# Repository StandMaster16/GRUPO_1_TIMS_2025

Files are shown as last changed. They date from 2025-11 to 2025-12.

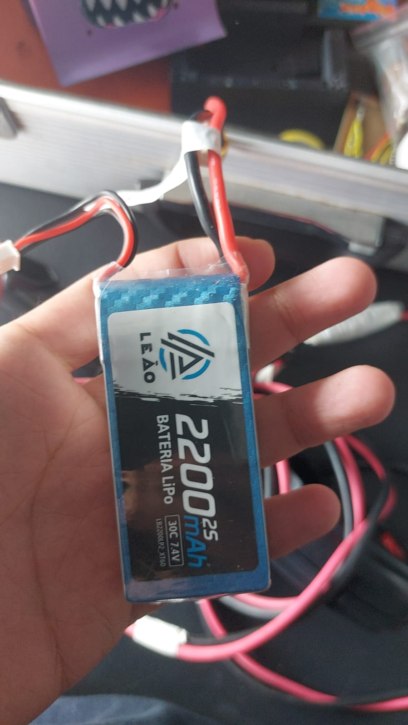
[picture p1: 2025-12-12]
electronics/img/Semana 1/bateria que vamos usar.jpg

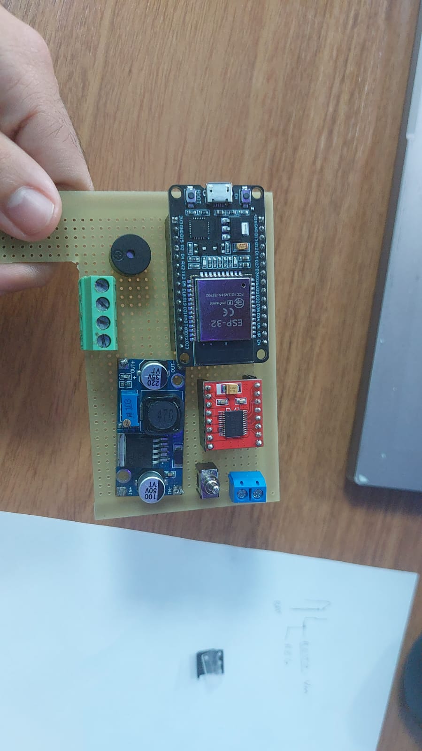
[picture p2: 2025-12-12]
electronics/img/Semana 7/primeiro arranjo.jpg

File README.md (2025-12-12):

# *Mini sumô - Sr. Batata*

Esse é o repositório online do projeto de mini sumô da equipe 1 do torneio interno do Grupo de Estudo Aplicado à Robótica (GEAR) em 2025.

## Equipe

- Gestão: Vitória Rodrigues
- Programação: Gabriel Matos
- Mecânica: David Praciano
- Eletrônica: Matheus Eduardo 
- Veterano: Vinicius Azevedo

## Organização dos Diretórios
```
GRUPO_1_TIMS/
|
├── code/                       # Implementação da programação
│
├── docs/                       # Documentação do código
│
├── electronics/                # Eletrônica do projeto
│
├── mechanics/                  # Mecânica do projeto
│
└── README.md --> ESTE ARQUIVO  # Resumo geral dos diretórios
```

Cada pasta contém um README interno com instruções específicas de uso, dependências e explicações específicas.

## Por quê "Sr. Batata"?

O ponto de partida do projeto mecânico foi a fase de brainstorming, que gerou inúmeras ideias de design. Para permitir a experimentação de todas as sugestões sem comprometer o protótipo base, a equipe decidiu por um robô desmontável.
Inspirado no conceito do brinquedo Toy Story, o robô foi batizado de "Sr. Batata", onde o chassi principal (a "batata") serviria como corpo base, e os acessórios seriam incrementos removíveis (como braços, chapéus e sapatos). A ideia era que, se um incremento não funcionasse em combate, bastaria desencaixá-lo e substituí-lo, agilizando a iteração de design.

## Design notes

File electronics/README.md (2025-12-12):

# Diretório de Eletrônica

## Como está organizado?

Em tese, tudo está na pasta `img/`, que contém um histórico de evolução do trabalho
de eletrônica do nosso mini sumô. Há um pequeno salto entre as semanas, por motivos
diversos, por exemplo: não tiramos foto de tudo. Porém, o que foi registrado e é 
pertinente, você com certeza vai encontrar lá.

## Um pouco sobre o circuito

O circuito do mini sumô "Sr. Batata" possui uma história interessante: Nasceu como um
simples arranjo de controlador, ponte H e motores, para uma máquina mortífera de 
controlador, ponte H, motores e algumas coisinhas.

## Como ele funciona?

### Componentes:

 - Dois motores n20 300 rpm
 - Uma ESP32
 - Uma ponte H TB6612FNG
 - Um buzzer passivo
 - Um controlador de tensão (AMS1117 ou o Buck Converter (ainda não foi decidido (11/12/25)))
 - Placa fenolite universal
 - Três KRE Borne
 - Barramento de pinos
 - Um switch alavanca

### Descrição:

A alimentação está ligada ao switch, a qual envia energia para a ponte H pela porta VM, que alimenta os motores A e B. A mesma alimentação é enviada ao regulador de tensão que converte 7.4v para 5v na porta VIM da ESP32. Os motores A e B estão ligados às respectivas portas OUT da ponte H, sendo as portas IN e PWM ligadas à ESP32. Por fim, o buzzer passivo conecta-se à ESP32

### Mural de conexões

- Positivo da Bateria -> L2 (switch)
- COM (switch) -> VM (TB6612FNG)
- A01 (TB6612FNG) -> Negativo do motor A
- A02 (TB6612FNG) -> Positivo do motor A
- B01 (TB6612FNG) -> Negativo do motor B
- B02 (TB6612FNG) -> Positivo do motor B
- D13 (ESP32) -> PWMA (TB6612FNG)
- D14 (ESP32) -> PWMB (TB6612FNG)
- D27 (ESP32) -> BI1 (TB6612FNG)
- D26 (ESP32) -> BI2 (TB6612FNG)
- D25 (ESP32) -> AI1 (TB6612FNG)
- D24 (ESP32) -> AI2 (TB6612FNG)

#### Para versão com AM1117 5V

- VIM (AMS1117) -> COM (switch)
- VOUT (AMS1117) -> VIM (ESP32)
- GND (AMS1117) -> GND (ESP32)
  
#### Para versão com Buck Converter

- IN+ -> COM (switch)
- IN- -> Negativo da Bateria
- OUT+ -> VIM (ESP32)
- OUT- -> GND (ESP32)

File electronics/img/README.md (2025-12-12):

# Diretório de Imagem de Eletrônica

O diretório está dividido em semanas, com registros visuais
de cada progresso feito em cada semana, além dos circuitos
feitos na plataforma CIRKIT IDE

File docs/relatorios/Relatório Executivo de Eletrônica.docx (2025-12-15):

RELATÓRIO DE ANDAMENTO DE ELETRÔNICA

RESPONSÁVEL TÉCNICO: Matheus Eduardo

PROJETO : Robô Mini Sumô Sr. Batata

PERÍODO: 28.11 a 12.12

CONCEITO E DEFINIÇÃO DA ARQUITETURA ELETRÔNICA

A premissa fundamental do robô Sr. Batata era a força para ser dominante no combate. Essa prioridade orientou a escolha de todos os componentes eletrônicos, buscando garantir a máxima potência e eficiência.

Pesquisa e Referências: O Matheus iniciou a fase de pesquisa nos sites das principais lojas de robótica do mundo (indicação do Vini), buscando inspiração e componentes em kits prontos e peças de mini sumô.

Escolha da Placa de Controle (MCU):

No dia 23/11, a equipe discutiu a escolha da placa de controle, com as seguintes considerações:

Opções | Análise | Decisão
STM32 | Conhecida como "o megazord das placas" por sua potência. Não havia experiência prévia em programação para ela | descartada.
ESP32 | Fortemente recomendada por um veterano (Célio) e mais familiar à equipe. | Selecionada. O repositório no Git foi criado utilizando a ESP32

SELEÇÃO DE COMPONENTES E TESTES INICIAIS

A escolha dos componentes foi fortemente baseada nas indicações de kits e peças das lojas de robótica que o Vinícius indicou.

Componentes | Especificação escolhida | Justificativa
motores | 2 modelos N20 de 300 RPM | Motores pequenos, com caixa de redução e os mais utilizados na categoria Mini Sumô.
Ponte H | TB6612FNJ | Embora necessitasse de um regulador de tensão (devido à bateria de alta voltagem), foi preferida em relação à L293D (que teria sido usada com 4 rodas).
Bateria | Lipo Battery 7.4v 2200 mAh | Recomendada por um veterano por proporcionar maior descarga de corrente. A tensão de 7,4V é enviada integralmente para os motores na potência máxima, garantindo o poder do robô.
Placa base | Placa fenolite (universal) perfurada de fibra de vidro | Usadas para montagem do circuito.
Conectores | XT60 (bateria), KRE borne (3) e barra de pinos | Para conexões de alimentação na placa principal

MARCOS DE TESTE (CIRCUITO EQUIVALENTE):

Data | Ação/Evento | Propósito e status
07.11 | Conclusão do esquema do circuito | O esquema do circuito já estava finalizado
07.11 | Testes dos motores no lab | Verificação funcional dos motores antes da montagem no chassi
14.11 | Montagem de um sistema eletrônico equivalente | Uso de componentes genéricos de laboratório para testes, simulando o sistema definitivo (motores, ESP, etc.)
02.12 | O Sr. Batata funciona (com circuito equivalente) | Comprovação da lógica do sistema antes da chegada/montagem das peças oficiais

DESAFIOS NA MONTAGEM OFICIAL

A transição para o circuito oficial foi marcada por desafios técnicos e de confiança, já que o responsável (Matheus) era da área de Programação, não de Eletrônica

Data | Evento/Desafio | Ação e impacto
Contínuo | Dificuldade na Disposição e Montagem: O responsável enfrentou dificuldades na disposição dos componentes no chassi. | O chassi de teste foi usado com componentes genéricos para validação da disposição.
14.11 | Aguardando Peças Oficiais: A equipe estava limitada, usando apenas peças do laboratório para montagem parcial. | Foco em montar o sistema eletrônico equivalente para adiantar os testes e a programação.
Todo o trajeto | Insegurança e Falta de Experiência (Soldagem): Matheus se sentiu inseguro com seu trabalho e inexperiente, especialmente na soldagem, que se tornou sua maior dificuldade. | A gestora ofereceu apoio contínuo. Ele recebeu ajuda e apoio de membros da própria equipe e de outras, o que aumentou sua confiança ao saber que outros programadores também atuavam na Eletrônica.
09.12 | Início da montagem do Circuito Oficial. | Com a confiança restabelecida e a lógica do circuito validada pelo modelo equivalente, Matheus iniciou a soldagem e montagem do circuito definitivo.
11.12 | Conclusão da Montagem do Circuito Oficial. | O circuito oficial foi finalizado a tempo para a integração com o chassi.

STATUS FINAL

O circuito equivalente cumpriu sua função de validar a lógica de potência e controle do Sr. Batata

Data | Marco alcançado | Estado atual (final) do projeto
11.12 | Circuito oficial finalizado | O circuito eletrônico principal está montado e pronto para ser integrado ao Chassi Oficial (que está em processo de impressão 3D, conforme o relatório de Mecânica)
12.12 | Integração física final e calibração de potência | O foco agora é na integração física com as partes mecânicas e no trabalho de Programação/Testes em campo

Anexos

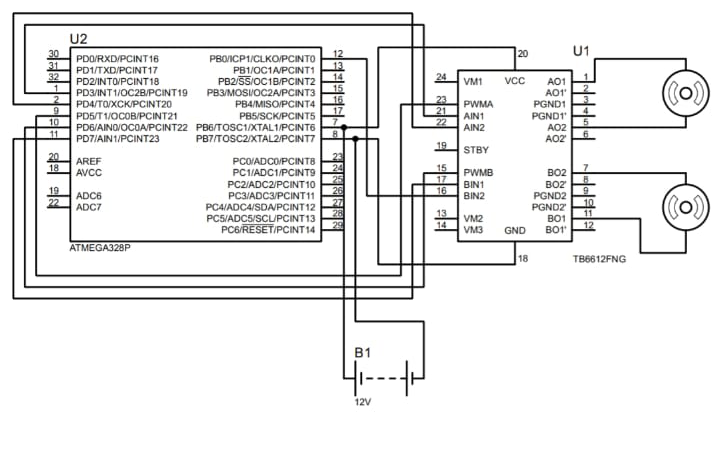
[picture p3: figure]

Anexo 1 - Circuito de esboço feito no proteus

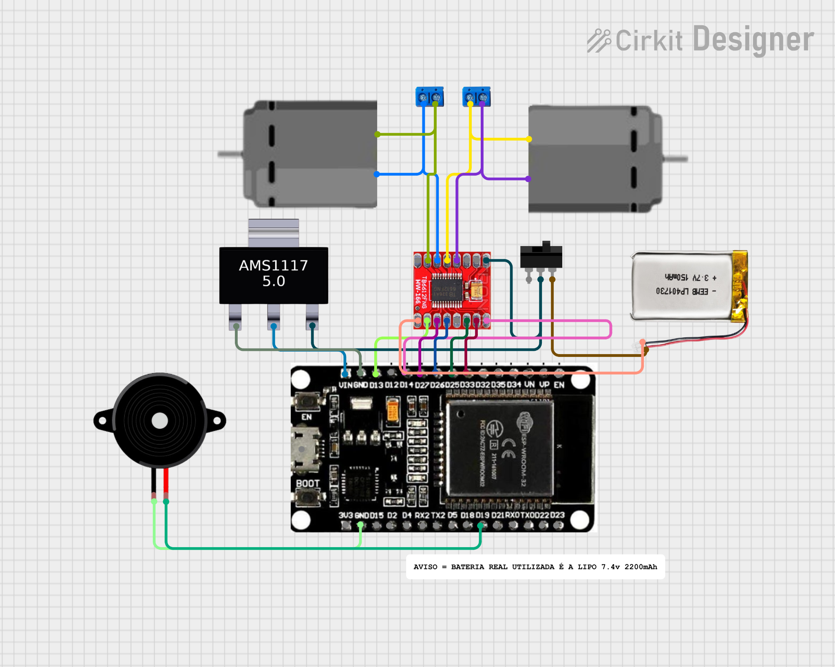
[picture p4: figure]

Anexo 2 - Modelo final 1 (usando AMS1117)

ESTE RELATÓRIO SERÁ ATUALIZADO CONTINUAMENTE PARA ACOMPANHAR A EVOLUÇÃO DA ÁREA ELETRÔNICA DO SR BATATA ATÉ O DIA DO TORNEIO (12.12)

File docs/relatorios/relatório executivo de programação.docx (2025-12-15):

RELATÓRIO DE ANDAMENTO DA PROGRAMAÇÃO

RESPONSÁVEL TÉCNICO:Couto Gabriel

PROJETO: Robô Mini Sumô Sr. Batata

PERÍODO: 28.11 a 12.12

PESQUISA, ALINHAMENTO E DEFINIÇÃO DO CONTROLE

O trabalho de programação começou com uma fase intensa de pesquisa nas duas primeiras semanas, utilizando os sites e vídeos indicados pelo Vinícius para definir a melhor arquitetura de código.

Mês | Ação geral
Outubro | O primeiro foco foi na escolha do controle. Embora a equipe inicialmente considerasse testar o uso de um aplicativo e um controle remoto, a decisão final foi priorizar o Controle Remoto para maior precisão e familiaridade, com o controle sendo reservado no dia 31 de Outubro.
Novembro | A equipe pegou uma ESP genérica para iniciar a fase de testes práticos do código. Em uma reunião de alinhamento entre as áreas, Praciano ajudou a definir a lógica de movimentação: o robô utilizaria o sistema Tank Drive, onde dois analógicos seriam usados para controlar a direção, com cada um controlando uma roda. Nesse mesmo dia, o código base já estava finalizado, embora apresentasse um erro de compilação no PlatformIO. A prioridade imediata passou a ser concluir o código de movimentação, buscando auxílio de Vinícius e outros veteranos para resolver a comunicação do controle com o ESP32.

DESENVOLVIMENTO DO CÓDIGO BASE E TESTES (10.11 a 17.11)

Um grande avanço ocorreu no dia 10 de novembro, quando o código base compilou 🙏. Com o problema de compilação resolvido, o foco passou para a validação funcional do sistema.

No dia 12 de Novembro, foi montado um circuito improvisado com LEDs para testar a comunicação entre a ESP e o controle. O teste foi bem-sucedido e o sistema se mostrou funcional. No entanto, foi notado que a deadzone do controle não estava ideal, sendo ajustada para evitar o drift. Infelizmente, dois LEDs foram queimados durante o processo.

Apesar do avanço, no dia 14 de Novembro, Gabriel ainda estava plotando o código na placa aos poucos, em processo de aprendizado. No dia 17 de Novembro, o programador ainda encontrava dificuldade em conectar o controle à placa microcontroladora.

O aprendizado técnico de Gabriel foi fortemente baseado na biblioteca Bluepad32 e no tutorial de Rachel De Barros (vídeo e site).

DETALHAMENTO DA LÓGICA DO CÓDIGO

O código desenvolvido por Gabriel utiliza a lógica de controle independente de cada motor. A seguir, uma análise do código funcional:

- Definição dos Pinos: O código inicia definindo a ligação física entre os pinos da ESP32 e a Ponte H.
- Controle de Movimento e Deadzone: Esta é a parte crucial do código. Ele usa a função ctl->axisY() para ler o movimento do analógico esquerdo.

AVANÇAR (roda esquerda):

if(ctl->axisY() >= 25) { // Se o analógico esquerdo for empurrado para frente

digitalWrite(A11, HIGH); // Define a direção (HIGH/LOW) para frente

digitalWrite(A12, LOW);

analogWrite(PWNA, 200); // Aciona o motor na velocidade 200

}

DEADZONE (garantia de parada)

if (ctl->axisY() > -25 && ctl->axisY() < 25) { // Se o analógico estiver na zona central

digitalWrite(A11, LOW); // Força a parada do motor

digitalWrite(A12, LOW);

}

Essa lógica de Deadzone (inicialmente em \pm 25, depois ajustada para \pm 75 no código final) foi fundamental para garantir que o robô pare completamente quando o analógico está em repouso, evitando o drift e garantindo maior controle no combate.

INTEGRAÇÃO E VALIDAÇÃO DO CIRCUITO EQUIVALENTE

Apesar das dificuldades iniciais com soldagem e o PlatformIO, a lógica do código foi validada em um sistema de teste:

- 29 de Novembro: Gabriel propôs usar uma Ponte H e motores antigos (genéricos) para testar o código, garantindo que a lógica de programação estivesse 100% funcional antes de Matheus integrar a eletrônica oficial.
- 05 de Dezembro: Durante os testes no circuito equivalente, o código foi validado com sucesso. No entanto, um imprevisto ocorreu (uma ponte H foi danificada, mas ressuscitou após um reparo) e foi observada uma inconsistência de propulsão (uma roda girando mais rápido que a outra), que a equipe se comprometeu a investigar na montagem final.
- 11 de Dezembro (Atualização do Código): O código mais recente já incorpora os aprendizados:
- A Deadzone foi ajustada de 70 para 75 e depois de 75 para 100, resolvendo o problema de drift do controle.
- Foi adicionada a Função Giro 360 (Zerinho Tokyo) no botão A, que inverte a direção de um dos motores, permitindo o giro rápido no próprio eixo, útil para reposicionamento tático.
- Foi implementado o Controle de Velocidade Variável (usando os botões Y para velocidade alta e X para velocidade baixa), permitindo que o robô use sua força total ou uma velocidade mais controlada.
- Foi adicionado um Sinal Sonoro (Buzzer) no botão B, que toca três vezes ao ser pressionado.

A área da programação do Sr Batata foi a com menos problemas e erros técnicos

por termos 2 programadores na equipe. Tivemos ajuda externa também e muito estudo por parte do Gabriel durante todo o andamento do projeto.

O restante do código na pasta de programação está totalmente comentado :

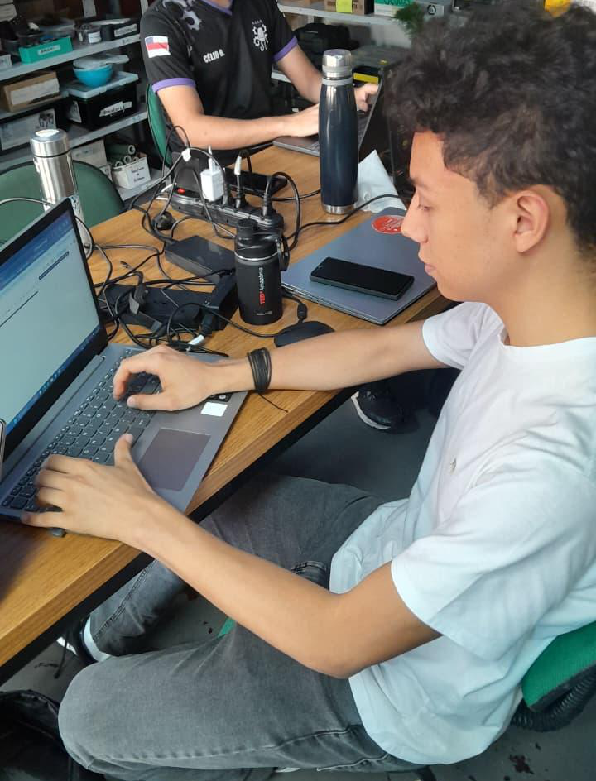
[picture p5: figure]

Gabriel trabalhando

ESTE RELATÓRIO SERÁ ATUALIZADO CONTINUAMENTE PARA ACOMPANHAR A EVOLUÇÃO DA ÁREA PROGRAMAÇÃO DO SR BATATA ATÉ O DIA DO TORNEIO (12.12)

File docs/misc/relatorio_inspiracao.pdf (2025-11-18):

UNIVERSIDADE DO ESTADO DO AMAZONAS ESCOLA SUPERIOR DE TECNOLOGIA GRUPO DE ESTUDOS APLICADOS À ROBÓTICA

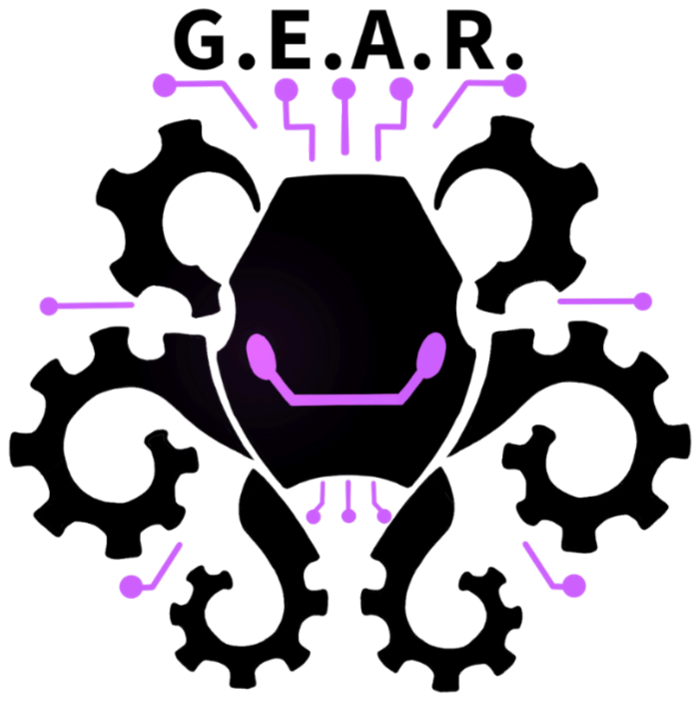
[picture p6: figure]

MINI SUMÔ

Manaus - AM
2025

RESUMO

O projeto teve como principal objetivo a confecção de robôs na modalidade mini

sumô, especificamente desenvolvidos para participar da competição Robocore 2025

em Brasília. Realizado por membros universitários, este projeto visou não apenas a

construção dos robôs, mas também proporcionar uma experiência prática e

aprofundada em áreas da engenharia, desde o trabalho em equipe, comunicação,

planejamento, design, testes até a execução. A participação na Robocore 2025

representou uma oportunidade valiosa, tendo em vista como sendo a primeira vez

que a liga acadêmica GEAR participa nesta modalidade. Além disso, foi uma

oportunidade valiosa para aplicar conhecimentos teóricos, desenvolver habilidades

multidisciplinares e fomentar o espírito de equipe e inovação entre os estudantes.

2

SUMÁRIO

3

### 1. INTRODUÇÃO

Este relatório detalha o desenvolvimento de dois robôs de mini sumô rádio

controlados de 500g, realizados por membros universitários do G.E.A.R.

(Grupo de Estudos Aplicados à Robótica). O objetivo principal foi projetar e

construir esses robôs para participar da competição Robocore Experience

2025. Este documento descreve todas as fases do projeto, desde o projeto

mecânico e eletrônico até a programação dos sistemas de controle. São

discutidos aspectos técnicos importantes, incluindo a comunicação Bluetooth

entre o microcontrolador e o controle remoto, os diagramas do circuito e as

considerações para o gerenciamento de energia. Em sua primeira

participação nesta categoria, a equipe conquistou o 15º e o 18º lugar de 20

competidores.

4

### 2. REFERENCIAL TEÓRICO

Mecânica:

- Modelagem do robô: Foi utilizado o software de CAD 3D Autodesk Inventor para realizar todas as medições dos componentes eletrônicos que seriam utilizados, o esboço do projeto e, por fim, a sua modelagem final. Aspectos de como os componentes seriam organizados para que o centro de massa fosse concentrado um pouco mais à frente do meio do robô, como estaria a sua distribuição de peso e o custo do material que seria utilizado foram considerados.
- Impressão do robô: Nosso laboratório possui a impressora 3D da Creality, portanto, foi usado o software fatiador Creality Print. Nele foram definidos parâmetros como o tipo de preenchimento, a forma da impressão e o tipo de material. Nesta etapa houve várias tentativas de impressão até chegar ao modelo final.
- Chapa Metálica: Para a construção da chapa foi usado um material mais resistente, uma lâmina de aço de mais ou menos 20cm x 20cm fora utilizado para a produção da mesma. Utilizando ferramentas como uma tesoura de cortar para reduzir suas dimensões, uma mini retifica para retirar as rebarbas e lixar a chapa para deixá-la mais fina.
Este método, revisado depois da competição da RoboCore Experience, tornou-se inviável a nível de competição - visto que utilizam-se chapas fabricadas exclusivamente para robôs sumôs mini.

Eletrônica:

- Componentes utilizados no Mini Robô Sumô
- Microcontrolador ESP 32
- Baterias Li-ion 7,4v 3300mah Modelo 18650 Recarregável
- Drive Motor Ponte H Dupla L298N
- Motores JGA 25-370
- Buzzer Ativo 5v
- Chave Interruptor
- O projeto do mini robô sumô rádio controlado utiliza como núcleo de processamento a placa ESP32, um microcontrolador de arquitetura Xtensa dual-core, amplamente empregado em sistemas embarcados

5

devido à sua conectividade Wi-Fi e Bluetooth integrada, capacidade de processamento e número elevado de GPIOs (General Purpose Input/Output).

- A alimentação elétrica do sistema é gerenciada por meio de uma ponte H L298N, a qual, além de controlar a direção e a velocidade dos motores DC, possui um regulador de tensão interno pré-ajustado para fornecer 5
V. Esse regulador é responsável por alimentar a ESP32 e periféricos, como o buzzer ativo, que atua como sinalizador sonoro para indicar tanto a energização do circuito quanto a conexão estabelecida entre o robô e o controle remoto.
- Para tração, foram utilizados motores JGA, conectados diretamente à bateria Li-Po de 7,4 V, garantindo torque e velocidade adequados às exigências da competição. O controle do robô é realizado através de gamepads de PS4 e Xbox, via comunicação Bluetooth, em conformidade com as normas especificadas no regulamento do campeonato.
- A integração eletrônica descrita fornece a base para a atuação da equipe de programação, responsável pela implementação dos algoritmos que interpretam os sinais enviados pelos controles e convertem essas entradas em comandos para a ponte H e demais atuadores. Nesse contexto, podem ser empregados algoritmos de controle, como o BluePad 32 , para otimizar a resposta dos motores, além de rotinas para gerenciamento de estados do robô, comunicação Bluetooth e tratamento de eventos. Assim, o trabalho conjunto entre hardware e software assegura que o mini robô atue de forma eficiente, responsiva e em conformidade com os parâmetros da competição.

Programação:

- Sistema embarcado (Parte do Software): o sistema embarcado atuou como um receptor e interpretador dos comandos em tempo real. A programação foi robusta o suficiente para receber dados por rádio frequência, os processar rapidamente e acionar os atuadores (Motor e Buzzer) sem atrasos perceptíveis para o operador. Isso envolve a configuração de interrupções e o gerenciamento eficiente do loop principal no código para garantir o retorno. A escolha da linguagem C foi a ideal para essa atividade devido a eficiência e controle de hardware (ESP32).

6

- Comunicação via Rádio Frequência: o ESP32 possui um módulo Wi-Fi e Bluetooth integrado que pode ser configurado para comunicação por rádio frequência, como usamos controle de Xbox não houve a necessidade do módulo Wi-Fi, assim trabalhamos somente com o bluetooth. Estabelecemos um protocolo de comunicação entre o transmissor (Controle de Xbox) e o receptor (ESP32 do robô) para garantir que os dados fossem enviados e recebidos de forma decifrável. Uma comunicação exclusiva entre dois dispositivos, com o transmissor e receptor pelo emparelhamento via ID (Identificador do Transmissor), evitando interferência externa.
- Utilização de biblioteca para comunicação bluetooth da ESP32 com o controle: A biblioteca utilizada foi a Bluepad 32, do autor Ricardo Quesada, que permitiu que a placa pudesse se comunicar via Bluetooth com o controle de Xbox e de PS4. Essa biblioteca permite que placas como ESP32, ESP32 da linha S e Arduino, possam se conectar a diversos periféricos, como mouses, teclados e controles de Xbox, PS e Nintendo Switch, para diversos fins.

### 3. METODOLOGIA

A metodologia adotada para a construção dos robôs mini sumo foi estruturada para garantir um processo organizado e eficiente, desde o planejamento inicial até os ciclos de testes e melhorias.

### 1. Etapas de Desenvolvimento

O desenvolvimento dos robôs mini sumo seguiu um fluxo de trabalho interativo e adaptativo, buscando otimizar a colaboração da equipe e o progresso do projeto. As principais etapas incluíram:

### 1. Planejamento Inicial: Definição dos objetivos do projeto e das

estratégias gerais.

### 2. Levantamento de Requisitos: Detalhamento das funcionalidades e

especificações de cada robô.

### 3. Cronograma e Divisão de Tarefas 4. Projeto Mecânico: Concepção e construção da estrutura física do

mini robô sumô.

7

### 5. Projeto Eletrônico: Desenvolvimento dos circuitos e seleção dos

componentes eletrônicos.
6. Programação: Criação dos algoritmos de controle e inteligência.

### 2. Levantamento de Requisitos

A fase de levantamento de requisitos teve início com uma reunião entre todos os integrantes da equipe de mini sumo. Durante esse encontro, foram realizadas trocas de ideias e discussões para definir as especificações e funcionalidades de cada um dos quatro robôs mini sumo a serem construídos. O objetivo inicial era desenvolver dois mini sumôs RC e dois mini sumôs autônomos. Entretanto, ao final do projeto, foi possível desenvolver a construção de dois mini sumôs RC.

### 3. Cronograma e Divisão de Tarefas

O planejamento inicial incluiu a elaboração de um cronograma de atividades com base nas discussões da reunião inicial. Embora ferramentas como o Trello tenham sido consideradas pela gestão, a equipe adaptou-se a um acompanhamento direto via WhatsApp devido a dificuldades de uso por parte de alguns membros.

A equipe, composta por cinco membros e um líder, passou por uma reestruturação para otimizar a distribuição de responsabilidades:

- Divisão Inicial: Duas duplas e uma área de mecânica.
- Divisão Final por Áreas de Especialização: Eletrônica, Programação e Mecânica.

O monitoramento das atividades e o acompanhamento do progresso eram realizados por meio de relatórios semanais enviados via WhatsApp. Estes relatórios continham os seguintes tópicos:

- O que fizeram durante a semana: Detalhamento das atividades concluídas.
- O que irão fazer na próxima semana: Planejamento das próximas tarefas.
- Bloqueios: Identificação de qualquer impedimento ou desafio enfrentado.
- Andamento do projeto: Resumo geral do progresso.

O líder da equipe também atuava ativamente no monitoramento do projeto, prestando apoio e tirando dúvidas dos membros, garantindo que os obstáculos fossem superados rapidamente.

8

### 4. Projeto Mecânico

O projeto mecânico foi fundamental para a concepção e materialização da estrutura física dos robôs mini sumô. Esta etapa concentrou-se em um estudo aprofundado dos chassis tipicamente utilizados em competições dessa modalidade, buscando as melhores práticas para:

- Equilíbrio e Desenvolvimento: Foram exploradas estratégias para garantir a estabilidade do chassi, crucial para um bom desempenho em combate, permitindo que o robô mantivesse sua posição e executasse manobras eficazmente.
- Acoplamento de Componentes: A estrutura foi projetada para permitir o acoplamento seguro e otimizado de todos os componentes eletrônicos e mecânicos (motores, baterias, sensores, etc.), visando uma distribuição de peso eficiente e um design compacto.
- Controle do Atrito: Analisou-se o atrito gerado entre o robô e a arena, bem como entre os próprios componentes, para otimizar a tração e a movimentação do mini sumo, influenciando diretamente sua capacidade de empurrar o oponente.

### 5. Projeto eletrônico

O sistema eletrônico do mini robô sumô é responsável por receber os comandos do piloto via rádio, acionar os motores e executar as manobras previstas para o combate. O projeto foi desenvolvido em conformidade com as regras da competição, priorizando eficiência, baixo consumo de energia e resposta rápida.

Inicialmente, a dupla responsável simulou um circuito completo para o robô no software Fritzing, incluindo um módulo Regulador de Tensão Step Down LM2596.

9

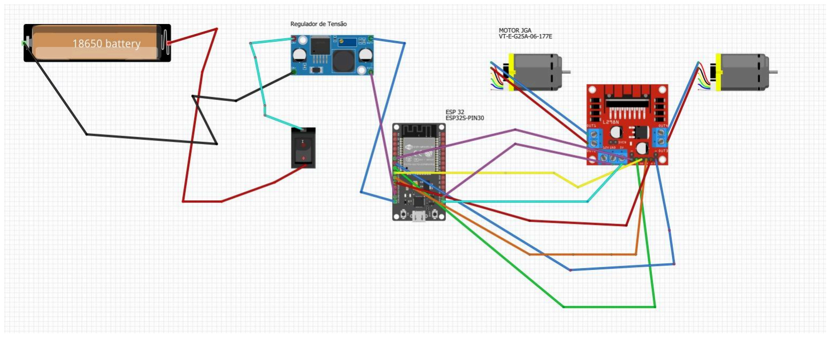
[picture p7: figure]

Dois pontos importantes considerados no projeto eletrônico do mini robô sumô foram:

1.Compatibilidade com as regras da competição: Todos os componentes e a disposição do circuito foram escolhidos para respeitar os limites de peso, dimensões e requisitos de segurança.

2.Integração dos componentes eletrônicos: Garantir a correta integração entre todos os componentes, como a bateria, o driver de motores, os motores DC e o microcontrolador ESP32. Essa integração assegura que as tensões e correntes estejam dentro dos limites operacionais de cada módulo, evitando sobrecargas, aquecimento excessivo ou falhas de comunicação.

Entretanto, ao longo da competição, foi observado que a ESP 32 suportava a tensão fornecida diretamente pela bateria e que o regulador gerava perdas e aumentava o peso do robô. Após análise, optou-se pela sua remoção, simplificando o circuito, diminuindo o número de conexões e eliminando um ponto potencial de falha.

### 6. Programação

A estrutura da lógica de programação foi simples, sendo a inteligência do robô residindo inteiramente na programação baseada na linguagem C/C++ que foi desenvolvida para o ESP 32, utilizando a Arduino IDE. Após estudos, a biblioteca bluepad 32 se mostrou mais versátil por permitir ao microcontrolador se conectar com uma gama maior de periféricos, ao contrário de bibliotecas como a PS4 Controller, que, como o nome sugere, só permite a conexão de controles de PS4.

Por conseguinte, a escolha da Arduino IDE também se deu pela sua facilidade de uso e fácil configuração, ao invés do VS Code (que aliás usa o framework da Arduino IDE através do PlataformIO para programação em Arduino) e da ESP-IDF, que apesar de permitir um controle maior do hardware, requer programação mais avançada e refinada, ou seja, de mais baixo nível de abstração.

Logo, por se tratar de uma biblioteca versátil, o controle do robô tornou-se mais fácil, pois não houve necessidade de projetar um joystick do zero, sendo utilizável no lugar controles populares de Xbox Series e Playstation 4, que são permitidos pelo regulamento da competição.

10

### 4. DESENVOLVIMENTO

- Estrutura mecânica

A modelagem do chassi em seu início foi trabalhosa por dois motivos principais: o tamanho dos motores JGA25-370 e da falta de um Placa de Circuito Impresso (PCI).

Um motor JGA25-370 combinado com o suporte e a roda somavam quase 100mm de comprimento, então um design para o robô partiu de uma ideia não convencional que foi deixá-lo disposto de uma forma antiparalela em relação ao outro motor. Isso possibilitou a integração dos motores, porém resultou em um centro de massa que classifica-se como um equilíbrio estático instável. A solução para amenizar tal impacto foi modelar o encaixe das baterias na frente do robô, projetando ele pra frente.

A falta de uma PCI resultou em um chassi bastante robusto e sem contornos, tendo uma aparência bastante cúbica e deixando-o no limite de seu peso (497g) e área (97mm x 95mm) prevista no edital: 500g e 100mm x 100mm.

Apesar disso, foi possível modelar, fatiar, imprimir e montar o robô sem muitos problemas. O espaço exigido pelos componentes foi atendido pela modelagem do robô e o problema do centro de massa foi diminuído pelo contrapeso das baterias e chapa metálica.

- Arquitetura eletrônica

A arquitetura eletrônica do mini robô sumô foi concebida de forma a garantir simplicidade. O sistema é composto pelo microcontrolador ESP32, responsável pelo processamento central e pela comunicação Bluetooth com os controles de PS4 e Xbox; pela ponte H L298N, utilizada para o acionamento bidirecional dos motores DC; pelos motores JGA25-370 (posteriormente reavaliados quanto ao peso); pela bateria Li-ion 7,4 V , que fornece a energia principal; além de um buzzer ativo 5 V, empregado como sinalizador sonoro, e de uma chave interruptora para desligar o circuito do robô .

- Sistema de alimentação

O sistema do robô é alimentado por uma bateria Li-Po de 7,4 V, utilizada tanto para a lógica quanto para a potência dos motores. A tensão da bateria é

11 aplicada diretamente ao terminal VMOT do driver L298N, responsável por alimentar os motores de corrente contínua. Para a parte lógica, não foi necessário o uso de reguladores externos, pois o próprio driver disponibiliza uma saída interna regulada de 5 V, utilizada para alimentar a ESP32. Dessa forma, a alimentação é simplificada, reduzindo a quantidade de componentes.Além disso, todos os terminais de GND foram conectados em um ponto comum, garantindo a referência elétrica única para o correto funcionamento do circuito e a comunicação estável entre ESP32 e driver.

- Lógica de Programação e Integração entre os Sistemas

Como discutido anteriormente, a lógica foi dividida da seguinte forma:

### 1. Comunicação por Rádio Controlado (Controle de Xbox)

O coração da operação do robô é a comunicação sem fio com o controle de Xbox. A programação ficou focada em:

### 1.1. Inicialização e Emparelhamento: O código inicia o módulo de

comunicação (Bluetooth Low Energy - BLE). Uma rotina foi implementada para procurar e estabelecer a conexão com o controle, quando a conexão é feita, o buzzer emite um som específico, fornecendo um feedback audível.

### 1.2. Decodificação de Dados: Uma vez conectado, o ESP32 envia dados

pelo controle. A programação inclui um parser para decodificar esses comandos, interpretando os estados dos botões e os valores dos eixos analógicos (joysticks) para determinar a direção e a velocidade dos motores. Tipo, os valores de X e Y de um joystick eram mapeados para o controle diferencial dos motores.

### 1.3. Restrição de Controle: Uma das principais regras da competição é

a de que o controle não pode se conectar a nenhum outro robô a não ser o do competidor. Esta restrição foi desenvolvida a partir da utilização mais avançada da biblioteca, através de uma função específica que lê um determinado parâmetro do periférico (o escolhido no projeto foi o PID – Product Identification), e o compara com o do periférico escolhido como único a ser pareado e retorna erro se for um dispositivo diferente, senão, o periférico irá se conectar e ter controle das funções. Foram realizados testes com resultados satisfatórios, nos quais controles diferentes do que havia sido pré-determinado via código se conectaram, mas não exerciam nenhum controle sob o robô, confirmando a restrição.

### 2. Controle de Atuadores (Motores N20)

12

A lógica de movimentação do robô foi desenvolvida para ser precisa e responsiva aos comandos do controle:

### 2.1. Mapeamento de Comandos: Os valores decodificados dos

joysticks são traduzidos em sinais PWM (Pulse Width Modulation) para cada motor. Houve a implementação de um algoritmo para converter as entradas X e Y do joystick em velocidades individuais para o motor esquerdo e direito, permitindo manobras como avançar, recuar, girar no próprio eixo e realizar curvas.

### 2.2. Controle de Velocidade e Direção: A programação manipula os

pinos GPIO conectados aos drivers de motor para controlar a direção de rotação e utiliza as funções de analogWrite() para variar o ciclo de trabalho do PWM, controlando a velocidade de forma suave e proporcional à inclinação do joystick.

### 3. Feedback Sonoro (Buzzer)

O buzzer foi programado para fornecer informações importantes como previsto pelo edital:

### 3.1. Indicação de Ligado: Ao energizar o robô, o código inicia com um

som tocado pelo buzzer, confirmando que o sistema embarcado está ativo.

### 3.2. Confirmação de Conexão RC: Conforme mencionado, um som

distinto é emitido quando o robô se conecta ao controle de Xbox, indicando que está pronto para receber comandos.

- Desafios enfrentados e soluções aplicadas

### 1. Problemas de Conectividade: Em alguns momentos, a conexão por rádio

frequência se mostrava instável. Para resolver isso, retardamos o acionamento do sinal feito por um dos joysticks para ganharmos tempo de conexão. Ajustes nos parâmetros de emparelhamento também foram explorados.

### 2. Latência na Comunicação RF: Inicialmente, notamos um pequeno atraso

entre o comando no controle e a resposta do robô. A solução envolveu a otimização do loop principal do código e também o “ponto morto” garantindo que a leitura dos dados por RF fosse prioritária e não fosse bloqueada por outras operações. Além disso, ajustamos a frequência de atualização dos dados no lado do controle e a taxa de amostragem no ESP32.

13

### 5. RESULTADOS PRELIMINARES

- Mecânica
O início dos testes para observar os resultados preliminares foi de extrema importância para analisar todo o desempenho físico por parte do mini robô sumô, nesta fase buscava-se:
1. Chassi: analisar se o material usado para modelar o robô suportaria o estresse mecânico que o mesmo estava sujeito, realizando testes que simulavam o peso do robô adversário. O resultado foi satisfatório, o material usado mostrou-se resistente aos embates em diferentes tipos de materiais usados;

### 2. Chapa metálica: testemunhar se a chapa estava adequada para oferecer

uma melhor rampagem e se estava bem fixada. Os testes haviam mostrado que o robô conseguia rampar os robôs simulados por objetos que haviam no laboratório;

### 3. Espaço para os componentes: testar se o espaço fornecido para os

componentes estava adequado a modo que não houvesse danos e se os mesmos não alterariam o centro de massa do robô. A observação preliminar ressaltou a dificuldade de organizar a quantidade de componentes eletrônicos dentro do chassi permitido pelo edital, resultando em um interior poluído visualmente, porém não o impedia de funcionar como o esperado.

- Eletrônica

Nos resultados preliminares, observou-se que a montagem eletrônica do mini robô sumô apresentou algumas limitações durante a competição. A ausência de uma placa de circuito impresso dificultou a organização do sistema elétrico, pois o uso excessivo de jumpers ocasionava falhas de contato.Esse tipo de montagem, embora funcional nos testes iniciais, não se mostrou o mais adequado para as exigências da competição, evidenciando a necessidade de um circuito otimizado e mais robusto para garantir maior confiabilidade.

Outro ponto relevante foi a escolha dos motores JGA25-370. Apesar de serem motores de alto torque, mostraram-se desvantajosos para a categoria de mini sumô, pois apresentavam peso elevado em relação ao tamanho reduzido e à agilidade exigida nos combates. Essa experiência permitiu concluir que a utilização de motores N20, mais leves e compactos, seria uma

14 alternativa mais adequada, equilibrando torque e velocidade com menor impacto no peso total do robô.

Para as próximas etapas, pretende-se redesenhar o sistema em uma placa dedicada, revisar a seleção dos motores e aprimorar a integração dos componentes, visando maior eficiência e competitividade.

- Programação

A fase de resultados preliminares foi crucial para validar a lógica de programação desenvolvida para o robô. Após a conclusão da montagem e da primeira versão do firmware, iniciamos os testes funcionais que focaram em:

### 1. Resposta aos Comandos por Rádio Controlado: Verificamos a latência

e a confiabilidade da comunicação entre o controle de Xbox e o ESP32. Ajustes na frequência de envio de comandos pelo controle e otimização na rotina de leitura e decodificação no robô foram implementados para minimizar qualquer atraso perceptível. Testes de alcance da comunicação também foram realizados para simular as condições da arena.

### 2. Controle de Motores: Realizamos testes para calibrar o mapeamento dos

valores do joystick para o PWM dos motores. O objetivo foi alcançar uma resposta de aceleração e direção suave e previsível. Inicialmente, observamos que o robô realizava movimentos bruscos. Para solucionar isso, implementamos uma curva de resposta não-linear no código, que suaviza as transições de velocidade e permite manobras mais precisas e controladas, essenciais para empurrar o oponente.

### 3. Feedback Sonoro do Buzzer: Confirmamos que os bipes de "ligado" e

"conectado" eram claros e funcionavam conforme programado, fornecendo um feedback audível e instantâneo.

### 4. Comportamento em Perda de Sinal: A perda de conexão foi o maior dos

problemas que tivemos, não solucionamos a perda de conexão, mas contornamos tardando essa perda de conexão. Como as lutas finalizaram em poucos segundos, não tivemos problemas por perda de conexão no campeonato.

15

### 6. RESULTADOS FINAIS

A participação da equipe na Robocore Experience 2025 resultou no 15º e 18º lugares, um desempenho que reflete o processo de aprendizado da equipe em sua primeira competição. O controle via Bluetooth e a resistência da estrutura mecânica foram pontos positivos. No entanto, o resultado foi negativamente impactado pelo peso excessivo dos motores JGA25-370 e pela montagem eletrônica com jumpers, que se mostrou pouco confiável durante os combates, indicando a necessidade de uma placa de circuito impresso.
A competição expôs uma lacuna entre o planejamento e o desempenho prático. O projeto inicial foi reduzido pela metade, focando em dois robôs rádio controlados em vez de quatro. A chapa metálica, eficaz em testes de laboratório, não performou bem contra adversários reais, e o sucesso na implementação da biblioteca de software Bluepad 32 contrasta com as dificuldades de hardware. Isso demonstrou a importância da adaptação e revelou pontos fortes e fracos do projeto.
Os aprendizados obtidos foram o resultado mais importante da experiência. Ficou claro que, para o futuro, é crucial otimizar o peso utilizando motores mais leves como o N20, desenvolver uma placa de circuito impresso para maior confiabilidade e aprimorar o design mecânico para um centro de massa mais estável. A gestão do projeto também foi identificada como um ponto de melhoria. A competição funcionou como um diagnóstico, oferecendo um direcionamento claro para futuras melhorias técnicas e organizacionais.

### 7. CONCLUSÃO

O desenvolvimento do mini sumô foi uma experiência desafiadora e, ao mesmo tempo, muito enriquecedora para a equipe. Tivemos que lidar com a dificuldade de conciliar os horários de todos, já que muitos tinham aulas e provas no mesmo período. Isso atrasou algumas etapas e, em certos momentos, quase paralisou o andamento do projeto. Esse desafio nos mostrou a importância de planejar melhor o tempo e buscar alternativas.

A participação na competição foi um ponto marcante, pois permitiu colocar em prática todo o esforço investido e visualizar, de forma clara, os resultados do nosso trabalho. Durante o torneio, conseguimos perceber os aspectos que precisam de melhorias, essa experiência prática foi fundamental para entender onde podemos evoluir, seja na parte técnica, como ajustes de programação e mecânica.

16

Mais do que os resultados, o aprendizado coletivo foi o maior ganho. A comunicação, a cooperação e a superação das dificuldades mostraram o potencial da equipe para enfrentar novos desafios. A competição não foi apenas uma oportunidade de mostrar o robô, mas também de crescer como grupo e já pensar em melhorias para futuros projetos, com mais foco, organização e confiança.

### 8. REFERÊNCIAS

QUESADA, Ricardo. bluepad32: Joystick, Gamepad and Bluetooth library for
ESP32 | and | Arduino | boards. | [Código-fonte]. | Disponível | em:
https://github.com/ricardoquesada/bluepad32. Acesso em: 30 abr. 2025.

SANTOS, Rui; SANTOS, Sara. ESP32 Pinout Reference: GPIOs. Random
Nerd | Tutorials, | [S. | l.], | 16 | jan. | 2024. | Disponível | em:
https://randomnerdtutorials.com/esp32-pinout-reference-gpios/. Acesso em: 29 mai. 2025.

DE BARROS, Rachel. Connect Your Game Controller to an ESP32: The Complete Guide. Rachel De Barros, [S. l.], [2025]. Disponível em: https://racheldebarros.com/connect-your-game-controller-to-an-esp32/. Acesso em: 15 abr. 2025.

NERY, GUSTAVO. Guia Definitivo de uso da Ponte H L298N. Blog Eletrogate,
5 | mar. | 2020. | Atualizado | em: | 1º | set. | 2022. | Disponível | em:
https://blog.eletrogate.com/guia-definitivo-de-uso-da-ponte-h-l298n. Acesso em: 20 mai. 2025.

Manaus, 7 de setembro de 2025

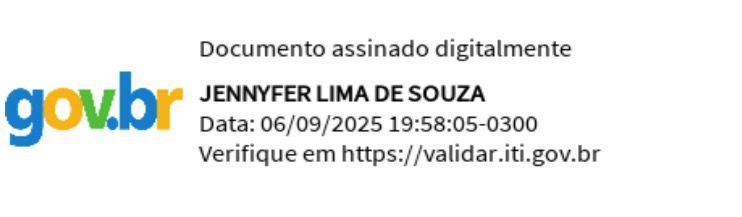
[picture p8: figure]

________________________________________________ Jennyfer Lima De Souza

17

________________________________________________ Cássio Pacheco Reis Lima

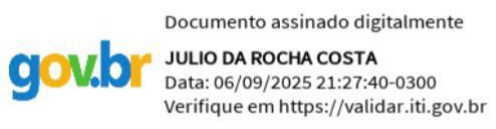
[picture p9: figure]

________________________________________________ Júlio Da Rocha Costa

________________________________________________ Ana Paula Monteiro Coelho

________________________________________________ Suely Amélia Casilla Nina

________________________________________________ Gabriele Lima De Souza

________________________________________________ Eduardo Araújo De Oliveira

___________________________________________________

18

Almir Kimura Junior

___________________________________________________ Samya De Castro Carvalho

19

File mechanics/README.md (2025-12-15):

## Diretório de Mecânica

Aqui se encontra imagens e os modelos 3D do Sr. Batata

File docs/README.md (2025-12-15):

## Diretório de Documentação

Este diretório tem como objetivo documentar o projeto do código do robô do seu grupo. É o relatório de todo o projeto.
Made by Vitória

O código implementado pode ser visto em: [`code`](../code).

## Estrutura do diretório

- `/atas` - Aqui fica as atas
- `/img` - Aqui fica mídias diversas
- `/misc` - Aqui fica alguns documentos que não se encaixam em nenhuma classificação
- `/relatorios` - Aqui fica os relatórios de cada sub-equipe do projeto
- `/sprint` - Aqui fica os sprints feitos com o Célio e a equipe

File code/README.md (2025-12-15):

## Diretório de Programação

Esse diretório está estruturado para um projeto PlatformIO, no entanto, a plataforma utilizada foi o ArduinoIDE
Por conta disso, somente a pasta `/src` foi modificada propriamente

## Estrutura de Diretórios

O projeto está organizado da seguinte forma:

```
code/
├── .pio/               # Arquivos de compilação e firmware (gerado automaticamente, não está no git)
├── .vscode/            # Configurações do editor Visual Studio Code (gerado automaticamente, não está no git)
├── include/            # Arquivos de cabeçalho (.h) globais do projeto
├── lib/                # Bibliotecas privadas (específicas do projeto) e externas
├── src/                # Arquivos de código-fonte (.c, .cpp) da aplicação
├── test/               # Testes unitários para validação do código
├── platformio.ini      # Arquivo de configuração principal do PlatformIO
└── README.md           # Este arquivo de documentação
```

### Descrição

  * `├── .pio/`

      * Este diretório é gerenciado pelo PlatformIO e contém os arquivos de compilação, dependências baixadas e o firmware final (`.bin` ou `.hex`). **Ele deve ser ignorado pelo sistema de controle de versão (ex: .gitignore).**

  * `├── .vscode/`

      * Contém as configurações específicas para o editor Visual Studio Code, como definições do IntelliSense. Também é gerenciado automaticamente.

  * `├── include/`

      * Use este diretório para arquivos de cabeçalho (`.h`, `.hpp`) que precisam ser compartilhados entre diferentes partes do seu código-fonte em `src/`. Um exemplo clássico é um arquivo `config.h` com definições de pinos e constantes globais.

  * `├── lib/`

      * Local ideal para bibliotecas. Cada biblioteca deve estar em sua própria subpasta (ex: `lib/MySensorLib/`). O PlatformIO automaticamente compila e vincula essas bibliotecas ao projeto. É perfeito para encapsular e reutilizar código.

  * `├── src/`

      * O coração da sua aplicação. O código-fonte principal (`.c`, `.cpp`) reside aqui. O arquivo `main.cpp` (ou `main.c`), que contém as funções `setup()` e `loop()`, é o ponto de entrada do programa.

  * `├── test/`

      * Destinado aos testes unitários. O [PlatformIO Test Runner](https://docs.platformio.org/en/latest/advanced/unit-testing/index.html) procura e executa os testes localizados aqui, ajudando a garantir a qualidade e a confiabilidade do código.

  * `└── platformio.ini`
      * Este é o arquivo de configuração mais importante do projeto. Nele você define a placa-alvo (`board`), o framework (`framework`), as bibliotecas de que o projeto depende (`lib_deps`), as opções de compilação (`build_flags`) e as configurações de upload e monitoramento.

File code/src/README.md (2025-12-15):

Aqui se encontra o código utilizado no dia de batalha

O código utiliza a biblioteca Bluepad32 para conectividade com um controle de PS4 e faz a implementação da parte eletrônica do projeto.

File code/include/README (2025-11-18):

Este diretório é destinado aos arquivos de cabeçalho do projeto (*header files*).

Um arquivo de cabeçalho é um arquivo que contém declarações C e definições de macro a serem compartilhadas entre vários arquivos de código-fonte do projeto. Você solicita o uso de um arquivo de cabeçalho em seu arquivo de código-fonte do projeto (C, C++, etc) localizado na pasta `src`, incluindo-o com a diretiva de pré-processamento C `#include`.

```c
// src/main.c

#include "header.h"

int main (void)
{
  ...
}
```

Incluir um arquivo de cabeçalho produz os mesmos resultados que copiar o arquivo de cabeçalho em cada arquivo de código-fonte que precisa dele. Essa cópia seria demorada e propensa a erros. Com um arquivo de cabeçalho, as declarações relacionadas aparecem em um só lugar. Se precisarem ser alteradas, podem ser alteradas em um único local, e os programas que incluem o arquivo de cabeçalho usarão automaticamente a nova versão na próxima vez que forem recompilados. O arquivo de cabeçalho elimina o trabalho de encontrar e alterar todas as cópias, bem como o risco de uma falha em encontrar uma cópia resultar em inconsistências dentro de um programa.

Em C, a convenção é dar aos arquivos de cabeçalho nomes que terminam com `.h`.

Leia mais sobre o uso de arquivos de cabeçalho na documentação oficial do GCC:

  * Sintaxe de Inclusão
  * Operação de Inclusão
  * Cabeçalhos de Inclusão Única
  * Inclusões Computadas

[https://gcc.gnu.org/onlinedocs/cpp/Header-Files.html](https://gcc.gnu.org/onlinedocs/cpp/Header-Files.html)

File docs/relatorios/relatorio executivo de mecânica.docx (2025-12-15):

🔧 RELATÓRIO DE ANDAMENTO DE MECÂNICA

RESPONSÁVEL TÉCNICO: David Praciano

PROJETO: Robô mini sumô Sr Batata

PERÍODO: 28.11 a 12.12

CONCEITO E JUSTIFICATIVA DE NOME

Ideação Inicial e o "Sr. Batata"

O ponto de partida do projeto mecânico foi a fase de brainstorming, que gerou inúmeras ideias de design. Para permitir a experimentação de todas as sugestões sem comprometer o protótipo base, a equipe decidiu por um robô desmontável.

Inspirado no conceito do brinquedo Toy Story, o robô foi batizado de "Sr. Batata", onde o chassi principal (a "batata") serviria como corpo base, e os acessórios seriam incrementos removíveis (como braços, chapéus e sapatos). A ideia era que, se um incremento não funcionasse em combate, bastaria desencaixá-lo e substituí-lo, agilizando a iteração de design.

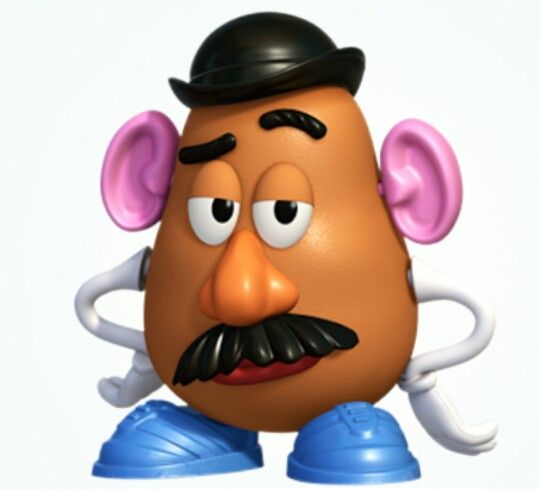
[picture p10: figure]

DESENVOLVIMENTO E ANÁLISE DAS RAMPAS

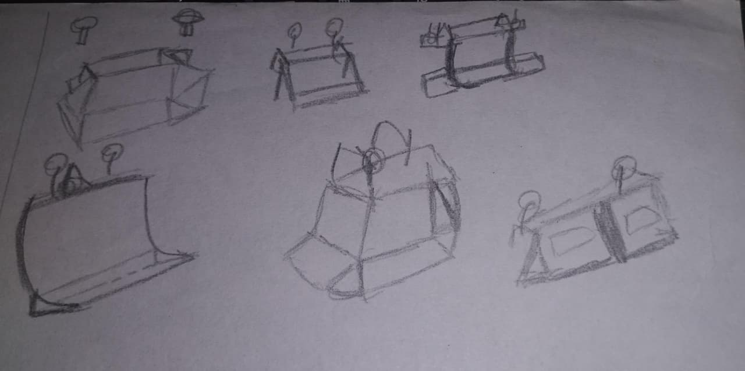
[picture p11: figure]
IDEIA INICIAL DAS RAM

OS 6 MODELOS DE RAMPA DO 1 CHASSI

RAMPA # | DESCRIÇÃO DA PROPOSTA | VIABILIDADE E ANÁLISE | STATUS FINAL (pré-impressão)
Rampa 1 | Rampa 3d complexa para cercear o campo de visão do oponente | Muito trabalhosa, com pontas que geravam potenciais pontos de tensão estrutural | Não viável
Rampa 2 | Rampa básica e simples | Modelagem direta e eficiente | Viável e implementada
Rampa 3 | Rampa básica com extensão lateral | Laterais abertas poderiam se tornar alvos fáceis para o adversário empurrar | Não viável
Rampa 4 | Rampa básica com curva acentuada | Integrada posteriormente no segundo modelo de chassi (fixo) | Viável (integrada)
Rampa 5 | Tronco com as três rampas integradas | Problemas de espaço e dificuldade de aplicação tática em combate | Não viável
Rampa 6 | Rampa com um “quebra-gelo” frontal para desviar a força adversária | Viável e modelada, mas não impressa na fase inicial | Viável (modelada)

Após alguns dias de análise, apenas as rampas 2 e 6 (que ao final dos sprints acabou sendo decidido ser fixo no corpo principal) foram consideradas promissoras pela equipe.

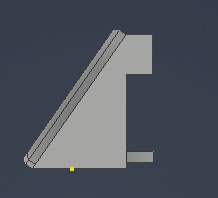
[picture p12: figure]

Rampa 2

DESAFIOS DE MODELAGEM E PERDA DE PROGRESSO

DATA | DESAFIO | AÇÃO E IMPACTO
07.11 | Bug crítico no notebook: Praciano perdeu TODO o progresso feito no chassi e rampas | O trabalho foi reiniciado do zero. Com o tempo escasso, a meta de criar um chassi de teste e um oficial foi abandonada. Foco no desenvolvimento de um único chassi oficial
Contínuo | Dificuldade na extrusão e montagem (inventor): Praciano enfrentou dificuldades na modelagem (extrusão de peças) e na montagem com o inventário | Houve solicitação de apoio a veteranos de mecânica, já que o nosso suporte primário (Vinícius) era da área de embarcados
17.11 | Superação técnica 🙏🏼: Praciano conseguiu superar as dificuldades de modelagem e finalmente executou a montagem completa | Significativa aceleração no processo, permitindo a finalização do design final

ANÁLISE E ITERAÇÃO DO PRIMEIRO PROTÓTIPO IMPRESSO

O primeiro modelo de chassi (mantendo o conceito desmontável do Sr. Batata com rampas removíveis e furos frontais estéticos) foi finalizado e enviado para impressão.

DATA | PROTÓTIPO E IMPRESSÃO | PROBLEMAS E CORREÇÕES | DECISÃO CRÍTICA
07.11 | Design inicial enviado para impressão | Problema 1: chassi ficou menor do que o esperado internamente para a acomodação dos componentes | -
10.11 | Cobrança do líder de embarcados sobre a impressão e acomodação de componentes | Problema 2: o chassi ultrapassou o limite externo de 10 cm do edital | -
11.11 | Ajustes: Verificação de erros nas rodas (aumento da altura para evitar contato com o chão, conforme o alerta do matheus) | Problema 3: Falta de parede de sustentação para os motores | O chassi foi impresso e as falhas foram confirmadas
14.11 | Sprint review (ponto de decisão): Debate sobre um possível novo modelo | Pautas levantadas: 1°: Rampa fixa seria mais fácil/melhor? (SIM) 2°: Quatro rodas seriam melhores? (NÃO) | DECISÃO 1: Abandonar o design desmontável e transicionar para um chassi fixo (mais viável e melhor aproveitamento do espaço interno) DECISÃO 2: Modelar um novo chassi maior internamente para caber os componentes

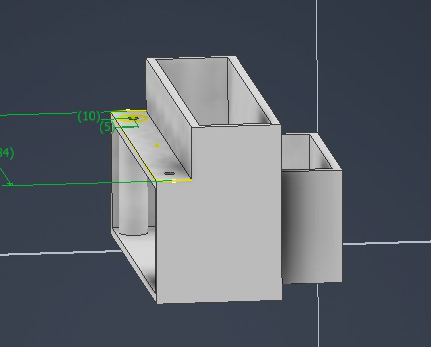
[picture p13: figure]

CHASSI INICIAL (MODELAGEM)

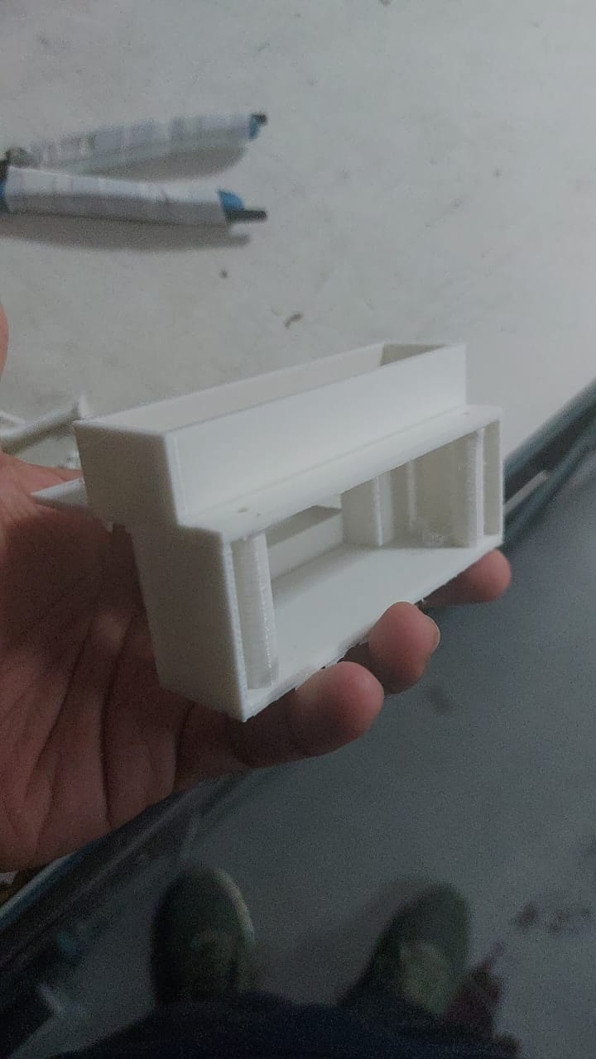
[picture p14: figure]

CHASSI INICIAL (IMPRESSO)

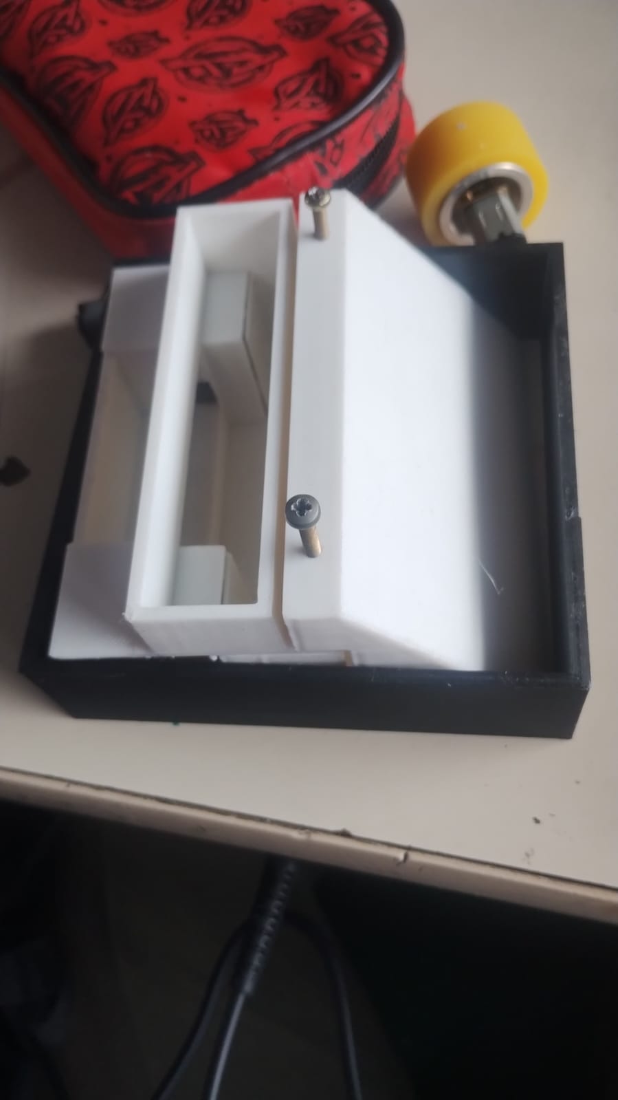
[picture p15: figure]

CHASSI INICIAL COM A RAMPA 2 PARAFUSADA

NO CORPO PRINCIPAL(passando do limite de 10 cm)

DESIGN FINAL E CHASSI OFICIAL

DATA | MARCO ALCANÇADO | ESTADO ATUAL DO PROJETO
24.11 | Novo chassi finalizado: modelagem do chassi fixo (corpo principal maior internamente e corrigido conforme as especificaçōes dos sprints anteriores) foi concluído e enviado para impressão | Este é o chassi oficial do sr batata, marcando o fim da fase de modelagem e iniciando a fase de integração
pós - 24.11 | Modelagem dos acessórios: iniciada a modelagem da armadura e do chapéu do sr batata | O robô final será fixo, possuindo uma armadura (funcionalidade mista: estética e proteção) e um chapéu (estético)

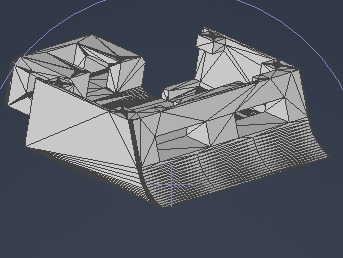
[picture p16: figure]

MODELAGEM FINAL

Este modelo foi encontrado na internet e modificado de acordo com algumas especificações e melhorias do antigo Sr Batata(a decisão de modificar um modelo pronto veio pelo pouco tempo que tínhamos para concluir a etapa de design)

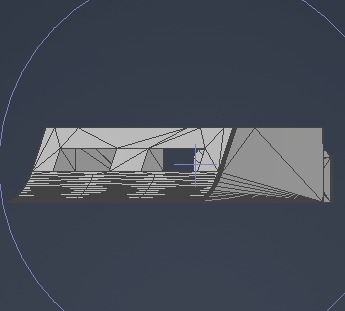
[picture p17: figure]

Vista de outro ângulo

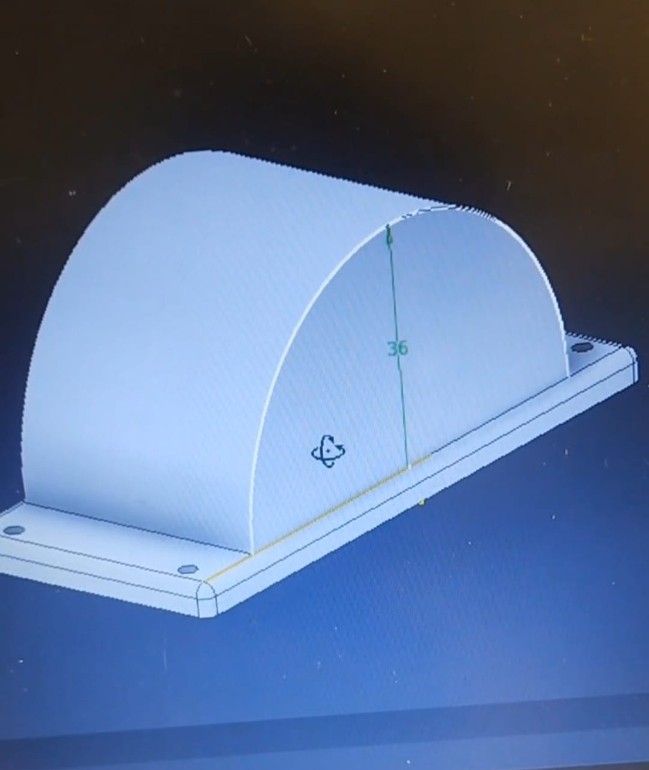
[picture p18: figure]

Modelagem do chapéu em andamento

STATUS ATUAL DA ÁREA (05.12): O Foco passa a ser o fim da modelagem dos acessórios de acordo com a verificação de encaixes e o trabalho de integração física com os componentes das áreas de eletrônica e programação

EVOLUÇÃO E ESTRUTURA FINAL DO SR BATATA PARA O TORNEIO (12.12)

A proposta inicial considerou um design modular e desmontável, composto por um corpo central e seis rampas de encaixe para facilitar a manutenção e a adaptação tática. A primeira iteração, denominada "Sr. Batata teste", demonstrou que a rampa removível comprometia a rigidez estrutural e a eficiência tática durante a competição. Diante dessa limitação, foi tomada a decisão de migrar para um chassi fixo.

Para otimizar o novo design, foi realizada uma pesquisa de referência e subsequente adaptação de um modelo existente. Após a aprovação da equipe, foi desenvolvida a armadura protetora com o objetivo de resguardar os componentes internos. Durante essa fase, surgiram desafios dimensionais na integração da armadura com a placa de circuito impresso (fenolite).

Para mitigar o conflito de espaço vertical, foi implementada a utilização de espaçadores para elevar a armadura, criando a folga necessária para o posicionamento adequado da fenolite sem comprometer a integridade dos componentes eletrônicos.

Com a questão da altura resolvida, o acabamento final consistiu na fixação das lâminas de ataque ao chassi utilizando adesivo de alta resistência (Tech Bond). Por fim, o posicionamento da fenolite foi ajustado e fixado.

Praciano ainda teve a ideia de imprimir um mini Sr Cabeça de Batata para ser o “piloto” do robô.

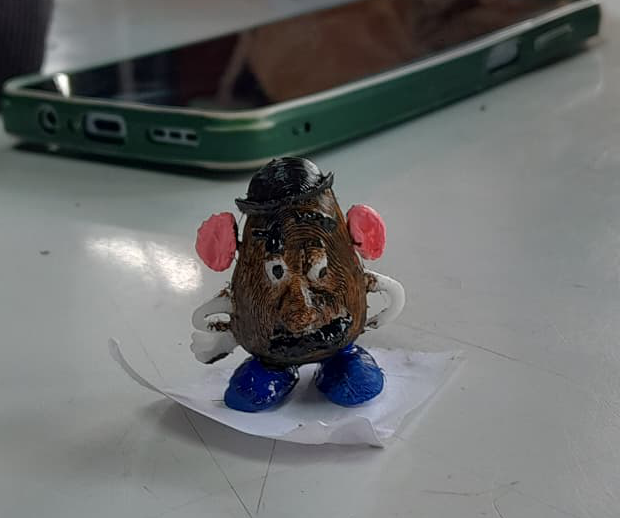
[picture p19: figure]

Sr Cabeça de Batata

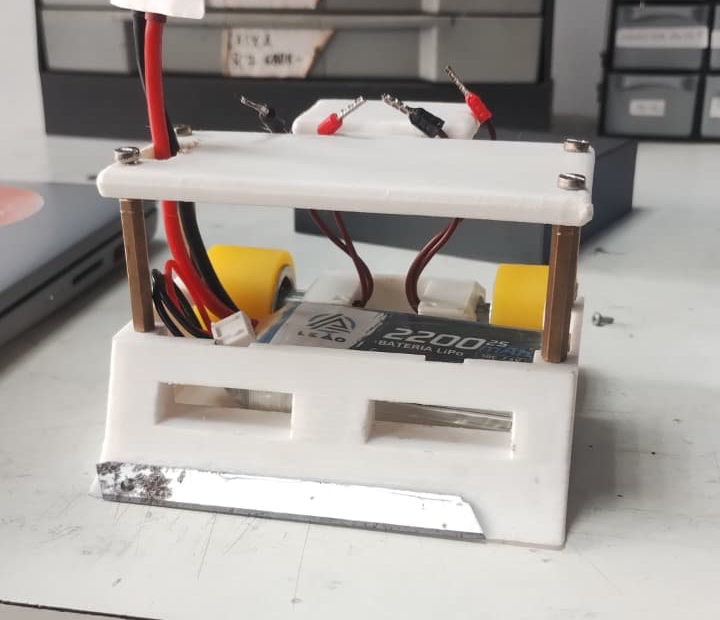
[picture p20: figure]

Modelo sem o circuito integrado

ESTE RELATÓRIO SERÁ ATUALIZADO CONTINUAMENTE PARA ACOMPANHAR A EVOLUÇÃO DA ÁREA MECÂNICA DO SR BATATA ATÉ O DIA DO TORNEIO (12.12).

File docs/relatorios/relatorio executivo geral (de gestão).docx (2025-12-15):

📝 RELATÓRIO EXECUTIVO GERAL DE ANDAMENTO DA EQUIPE 1

Sr Batata: 🥈 2° lugar no torneio interno GEAR 2025

Gestora: Vitória

Veterano/Técnico: Vinícius

Mecânica: Praciano

Eletrônica: Matheus

Programação: Gabriel

Meta Geral: Construir o robô Mini Sumo controlado por controle remoto, deixando a última semana apenas para testes e ajustes finais.

Data do Torneio: 12 de Dezembro (Remarcado)

O Sr. Batata superou muitos desafios logísticos e técnicos para conquistar o Segundo Lugar no torneio GEAR 2025. Minha gestão priorizou a motivação e o vínculo interpessoal em detrimento da rigidez hierárquica, focando na entrega de resultados tangíveis sobre a estrita burocracia.

VISÃO GERAL DO PROJETO E CRONOGRAMA

A Equipe 1 iniciou o projeto com a meta de ter o robô finalizado para testes até o início de dezembro. O cronograma enfrentou atrasos devido a compromissos pessoais, feriados e semanas de prova.

PERÍODO (SPRINT) | FOCO PRINCIPAL | STATUS GERAL
out. 28 - nov. 03 | Planejamento e pesquisa | Definição de papéis, início das pesquisas, e alinhamento presencial (nome do robô: Sr. Batata)
nov. 03 - nov. 17 | Design e aquisição | Definição final dos componentes, finalização da modelagem do primeiro chassi (teste ou definitivo). Início da programação de comunicação
nov. 17 - nov. 28 | Montagem teste e ajustes | Interrupção por feriados e provas. novo chassi definitivo enviado para impressão. Código de controle funcionando. componentes definitivos (eletrônica) recebidos
nov. 28 - dez. 05 | Montagem definitiva e ajustes | Finalização da montagem, foco imediato !!!

AVANÇOS POR ÁREA (PROGRESSO TÉCNICO):

Área | Marcos alcançados | Pendências e próximos passos
Mecânica | Chassi: dois modelos (teste e definitivo) foram concebidos. o modelo definitivo foi enviado para impressão 3D (Relatório 28/11). Documentação: Imagens das modelagens antigas e atuais enviadas (Relatório 28/11) | Montagem física final com o chassi impresso
Eletrônica | design: apresentação de pesquisas sobre placa controladora e circuito inicial. Aquisição: componentes críticos (motores N20, ponte H) definidos e componentes definitivos recebidos (Relatório 17/11) | Compra de uma nova placa ESP solicitada. Montagem e soldagem final do circuito definitivo
Programação | Código: Início da programação voltada à comunicação com o controle remoto. funcionalidade: código do controle funcionando com a placa (Relatório 28/11) | Integração do código principal (já pronto, mas não testado) com o robô físico

RETROSPECTIVA DESSA JORNADA

- Mecânica (Praciano)

Design Inicial e Pivô: Início com o chassi modular/desmontável. A equipe, sob análise, pivotou rapidamente para o chassi fixo devido a riscos de rigidez.

Desafio de Integração: Superação do conflito dimensional entre a armadura protetora e a fenolite, resolvido pelo uso de espaçadores.

Resultado Final: Estrutura robusta e estável, que suportou integralmente o estresse das batalhas do torneio.

- Eletrônica e Integração (Matheus)

Dificuldade Inicial: Existência de dúvidas sobre a soldagem e o manuseio da Fenolite e dos componentes (ESP32, Ponte H), gerando um "medo" inicial de falha.

Contribuição do Matheus: Foi essencial para a integração. Assumiu a responsabilidade pelo GitHub e ajudava muito todos os outros membros da equipe.

Resultado Final: Componentes integrados e funcionais.

- Programação (Gabriel)

Ajustes Críticos: Dedicação na resolução dos erros de compilação e, principalmente, na calibração fina da Deadzone (75 - 100), eliminando o drift do robô (pelo menos parte dele).

Tática: Implementação bem-sucedida das funções estratégicas: Giro 360 (Zerinho Tokyo no Botão A) e Controle de Velocidade Variável (PWM) de acordo com as vontades do Praciano.

Resultado Final: Software refinado e tático.

PONTOS E ESTILO DE GESTÃO

Fator de gestão | Ação | Impacto
Foco no vínculo | Priorização da comunicação empática e formação de laços de amizade sobre a cobrança estrita de relatórios. | Sincronia Elevada: Maior coesão e lealdade da equipe, fundamental para superar crises (vontade de desistir, absenteísmo)
Gerenciamento de crises | Suporte e compreensão durante períodos de baixa disponibilidade (doença da Gestora, desafios pessoais da equipe, absenteísmo do Vinícius) | Retenção de Membros: Evitou a perda de dois membros com vontade de desistir (por mais que eles estivessem pensando nisso em segredo); manteve alta energia focada na entrega
Cobranças por resultado | Ênfase na entrega de marcos funcionais do robô (código compilando, circuito funcionando, chassi estável) em vez de documentação excessiva | Eficiência Acelerada: Manteve o foco da equipe na engenharia em um cronograma apertado, resultando na entrega de um produto competitivo no prazo
Busca por apoio externo | Utilização de networking (comunicação com outras gestoras) e suporte familiar para validar decisões e definir a direção da equipe | Ações de gestão baseadas em insights de liderança experiente, evitando tantos erros de novato

EXTRA:

- O atraso no cronograma: o período de 17/11 a 28/11 gerou atrasos significativos devido a feriados e provas, exigindo um plano de compensação focado

Ação imediata: reuniões de duplas diárias e relatórios diários de progresso são mandatórios para a semana de 01/12 a 05/12.

- Documentação (GitHub): a organização do repositório com pastas de código, relatórios e esquemas era uma pendência desde 03/11. A atualização do github ainda estava em andamento em 28/11 (relatório 28/11).

Ação imediata: o github deve ser atualizado imediatamente com as modelagens de chassi e o modelo do circuito elétrico.

PLANO DE AÇÃO IMEDIATA PARA AS ÚLTIMAS DUAS SEMANAS

Dias reservados para montagem definitiva, testes e ajustes

Prioridade | Ação | Responsável | Prazo
Eletrônica | Montagem e soldagem de circuito definitivo | Matheus (com suporte do vinicius) | 05/12
Geral | Integração final do chassi impresso, eletrônica e programação | Todos | 05/12
Gestão | Relatórios de progressos diários | Todos | 12/12

DESAFIOS PESSOAIS E BUROCRÁTICOS

- Absenteísmo (Vinícius): Embora notado, a gestão permitiu que a equipe compensasse a lacuna, demonstrando resiliência (os membros gostavam de "se virar"e eu entendo o ponto do Vinicius, era bom pra evolução deles).
- GitHub: O GitHub foi percebido como "trabalhoso e complicado" pela maioria da equipe. A solução foi a delegação total da responsabilidade ao Matheus (foi feita uma reunião de atualização do git em conjunto com a gestora garantindo o registro sem sobrecarregar ninguém).

RESULTADO FINAL DA EQUIPE:

O sr batata foi um sucesso!! A equipe foi um sucesso!!! Conquistando o segundo lugar no torneio e vencendo 3 das 5 batalhas que participou.

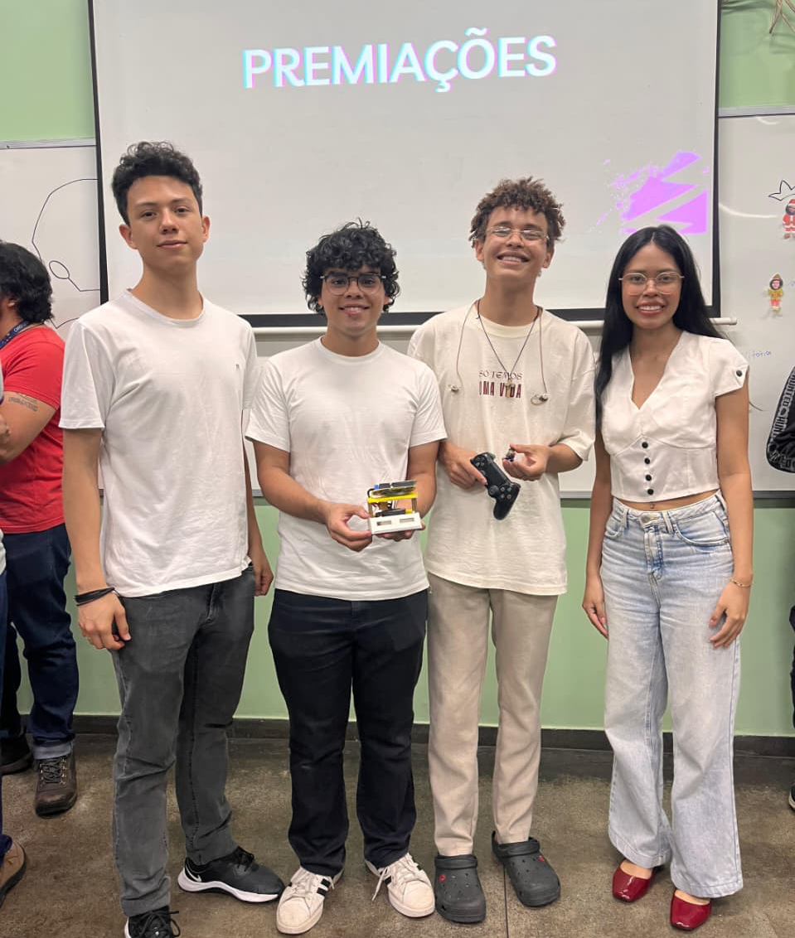
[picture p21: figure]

Equipe 1, torneio interno GEAR 2025

A Gestora manifesta grande satisfação com a experiência e a total disposição de trabalhar novamente com a equipe.

Recomendação para a Diretoria: O modelo de gestão que prioriza o vínculo interpessoal e a entrega de resultados tangíveis se mostra extremamente eficaz em projetos de inovação. Sugere-se considerar a inclusão de soft skills e gerenciamento de conflitos nos próximos treinamentos de liderança.

ESTE RELATÓRIO SERÁ ATUALIZADO CONTINUAMENTE PARA ACOMPANHAR A EVOLUÇÃO DA EQUIPE ATÉ O DIA DO TORNEIO (12.12)

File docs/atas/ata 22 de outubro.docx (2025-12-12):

# 📝 Ata da reunião | outubro, 22

EQUIPE 1

Gestão: Vitória

Veterano: Vinícius

- Organização final da equipe:

David - Mecânica;

Matheus - Eletrônica;

Gabriel - Programação;

- Situação atual do robô: A equipe realizou a primeira reunião de alinhamento. As funções foram definidas e o cronograma semanal de trabalho foi estruturado.

O projeto encontra-se na fase inicial de planejamento e pesquisa, com cada membro estudando a área pela qual ficou responsável (mecânica, eletrônica e programação).

- Método de Gestão escolhido pela equipe:

Decidimos adotar um modelo de gestão com metas semanais leves e colaborativas de acordo com a realidade do projeto, com:

- Vitória responsável pela coordenação e envio dos relatórios semanais à gestão;
- Cada integrante enviando seu progresso até sexta-feira à noite;
- Reuniões rápidas semanais (na quarta de forma online e na sexta de forma presencial) para revisar o andamento e redistribuir tarefas da semana seguinte;
- Uso do GitHub como central de arquivos e acompanhamento técnico (ideia do Célio), que ficou sob responsabilidade principal do Matheus;
- A última semana reservada para testes (28.10 até 05.11);
- Vinícius, veterano, oferece suporte técnico contínuo nas áreas de mecânica, eletrônica e programação.

### Próximas etapas:

Itens | Data de conclusão | Status
- Concluir/começar o design inicial do chassi - Selecionar e validar os componentes eletrônicos. - Criar o repositório GitHub e adicionar a estrutura do projeto em andamento. | 29.10 | 🔘 Não iniciado
TEORIA: - David: Mecânica - estrutura, chassi, encaixe dos componentes. - Matheus: Eletrônica - microcontrolador, bateria, motores, ponte H. - Gabriel: Programação - controle do robô, sensores, estratégia de ataque. - Vinícius: suporte geral e orientação técnica. | 29.10 | 🔵 Em andamento
Alinhamento da equipe | 22.10 | 🟢 Concluído

🔘 Não iniciado | 🔵 Em progresso | 🟢 Concluído

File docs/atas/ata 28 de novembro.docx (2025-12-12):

# 📝 Ata da reunião | novembro, 28

# Equipe 1 | Torneio Mini Sumo GEAR 2025

Entrega final (modificada) 12/12

Gestora: Vitória

Veterano: Vinícius

Equipe: Praciano (Mecânica), Matheus (Eletrônica), Gabriel (Programação)

Meta geral: construir um robô Mini Sumo controlado por controle remoto, deixando a última semana apenas para testes e ajustes finais.

PERÍODO: PERÍODO ABRANGIDO (Sprint): 17 a 28 de novembro (2 semanas)

data da reunião de acompanhamento: 28/11

formato: online

presentes: vitória, matheus, praciano

RESUMO DOS PERÍODOS

O período abrangido pela ata foi marcado por pausas significativas:

- 17/11 a 21/11: progresso reduzido devido a feriados (19 a 21) e compromissos pessoais.
- 24/11 a 28/11: pausa para a semana de provas da faculdade, foco em ajustes técnicos pontuais, sem grandes avanços na montagem :(

RELATÓRIOS INDIVIDUAIS (17/11 a 21/11):

membro | status (cumprimento dos objetivos) | dificuldades ou motivação | plano de compensação
praciano | conseguiu verificar a montagem do 1º chassi e encontrar o modelo do 2º chassi | falta de tempo devido a compromissos pessoais | foco total nas tarefas na quinta e sexta-feira (após as provas)
matheus | simm (conseguiu montar o circuito 🙏) | - | -
gabriel | não enviou o relatório solicitado | - | -

AJUSTES TÉCNICOS E AVANÇOS (24/11 a 28/11):

- eletrônica (matheus): foi identificada a necessidade de aquisição de uma nova placa ESP 32 para melhoria e estabilização do circuito
- programação (gabriel): foi reportado (pelo matheus) o sucesso na funcionalidade do código de controle, que faz a comunicação com a placa microcontroladora
- mecânica (praciano): o novo modelo de chassi definitivo foi enviado para impressão 3D. atualizações do github agora estão ok 😁

DIFICULDADES E DESAFIOS (da gestão):

- acompanhamento técnico (vinícius): a equipe sente a ausência e a dificuldade em contatar o veterano, principalmente para o acompanhamento técnico, na área de soldagem em eletrônica
- prazo crítico: temos apenas uma semana (01 a 05) para finalizar completamente a montagem do robô. a semana seguinte (última antes do torneio) deve ser dedicada exclusivamente a testes e ajustes.

PRÓXIMOS PASSOS:

ação | responsável | prazo | detalhes
montagem definitiva | todos (especialmente mecânica e eletrônica) | 05/11 | prioridade máxima: concluir a montagem de todos os subsistemas
acompanhamento | vinícius | - | agendamento pra ajudar na soldagem de componentes
compromisso com horários | todos | 01/11 a 05/11 | obrigatório: comprometimento com os horários das reuniões em duplas (segunda a quinta) e com a reunião geral (sexta)
relatórios diários | todos | diário | enviar relatórios diários (ao final do dia) detalhando o progresso e impedimentos na montagem

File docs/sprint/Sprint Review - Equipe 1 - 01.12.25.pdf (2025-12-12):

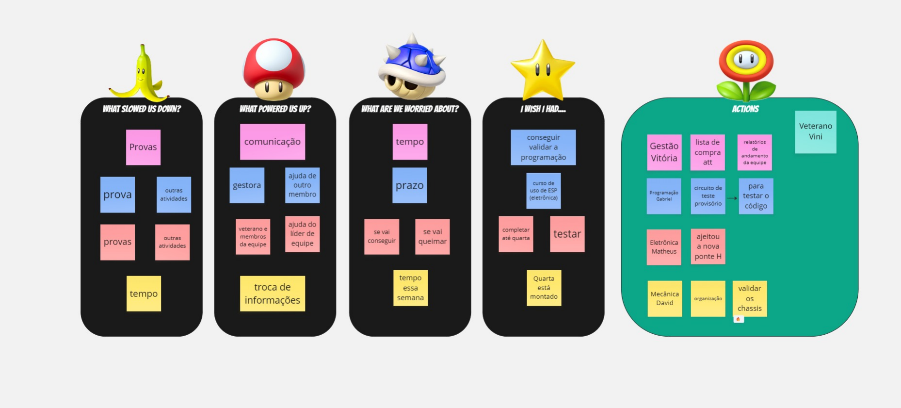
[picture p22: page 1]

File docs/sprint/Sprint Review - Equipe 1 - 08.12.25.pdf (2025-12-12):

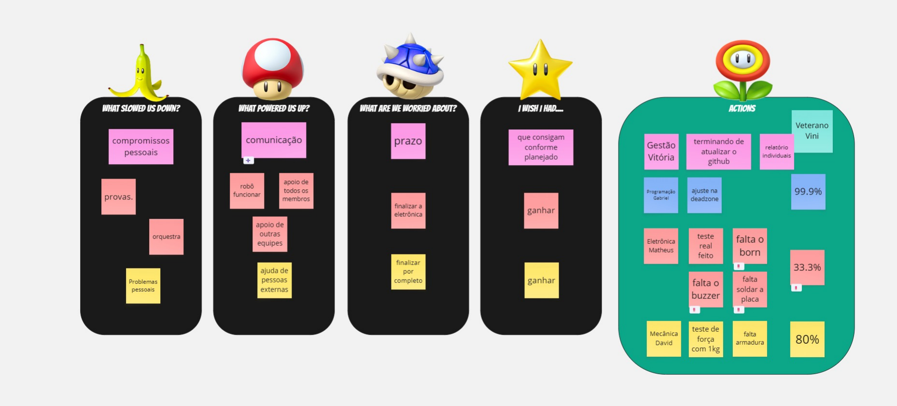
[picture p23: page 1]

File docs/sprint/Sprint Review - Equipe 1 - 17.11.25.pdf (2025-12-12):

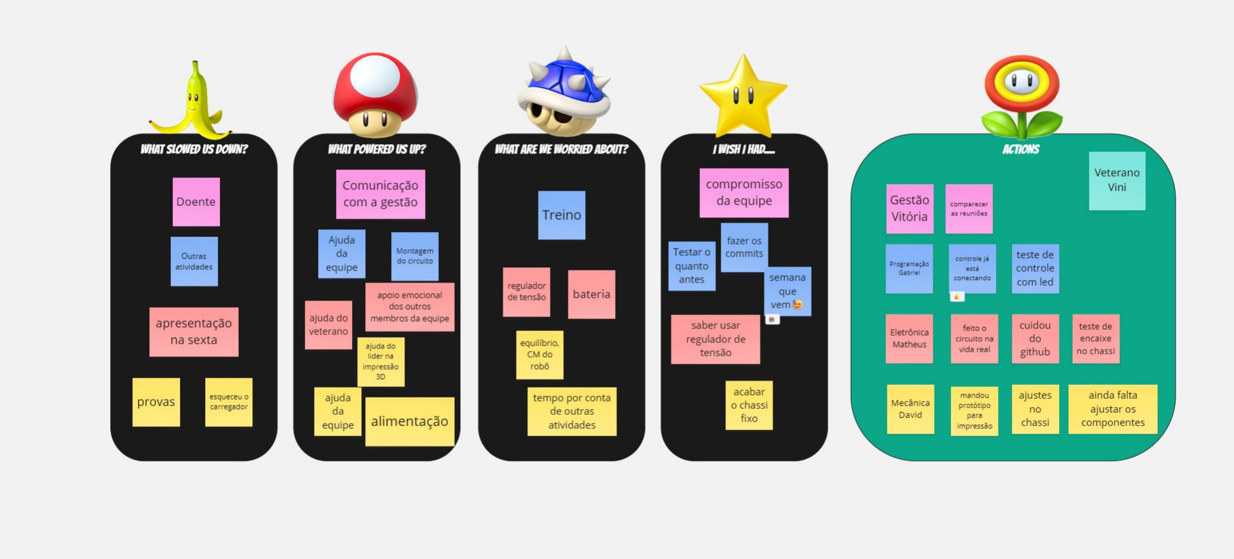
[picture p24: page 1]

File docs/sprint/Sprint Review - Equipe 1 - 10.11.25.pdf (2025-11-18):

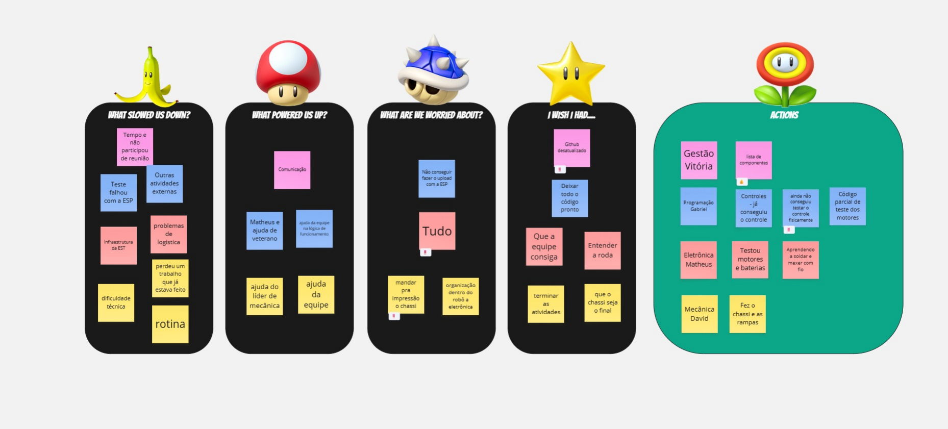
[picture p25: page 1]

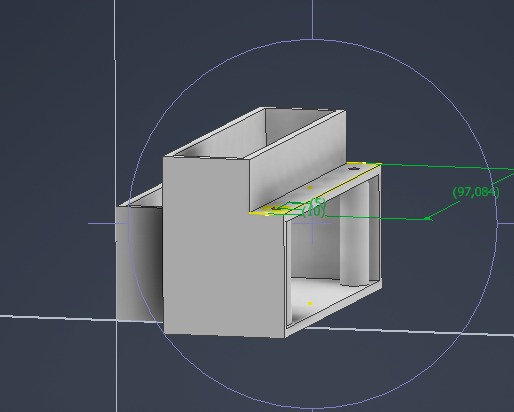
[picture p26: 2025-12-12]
mechanics/img/chassi 2.jpg

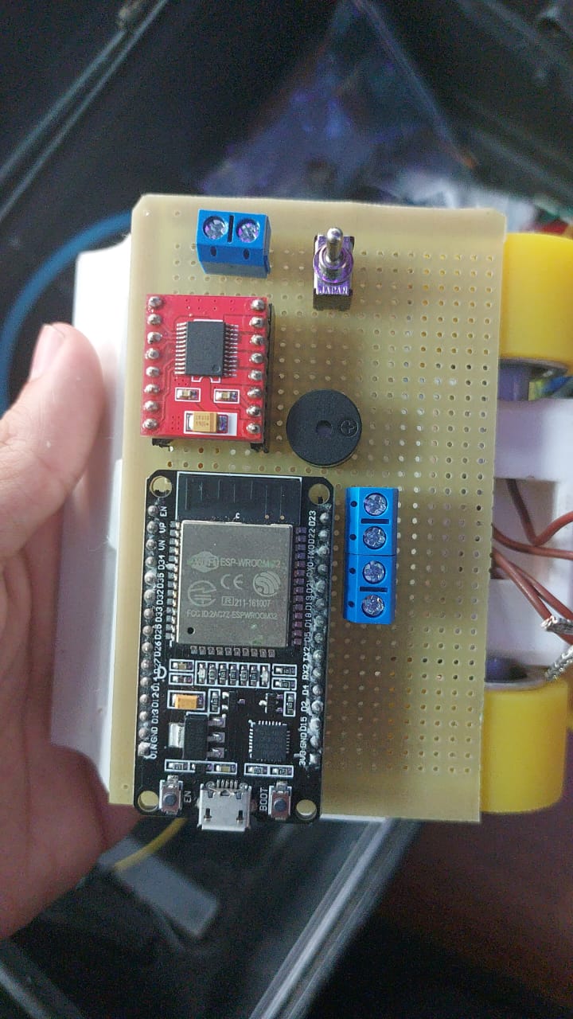
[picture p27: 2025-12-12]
electronics/img/Semana 7/segundo arranjo.jpg

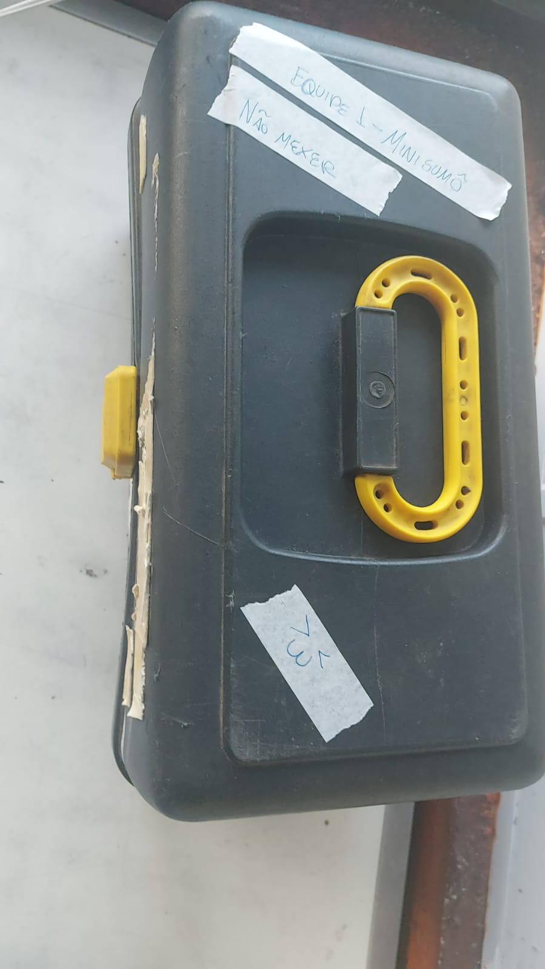
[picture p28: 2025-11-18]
electronics/img/Semana 2/nossa caixa.jpg

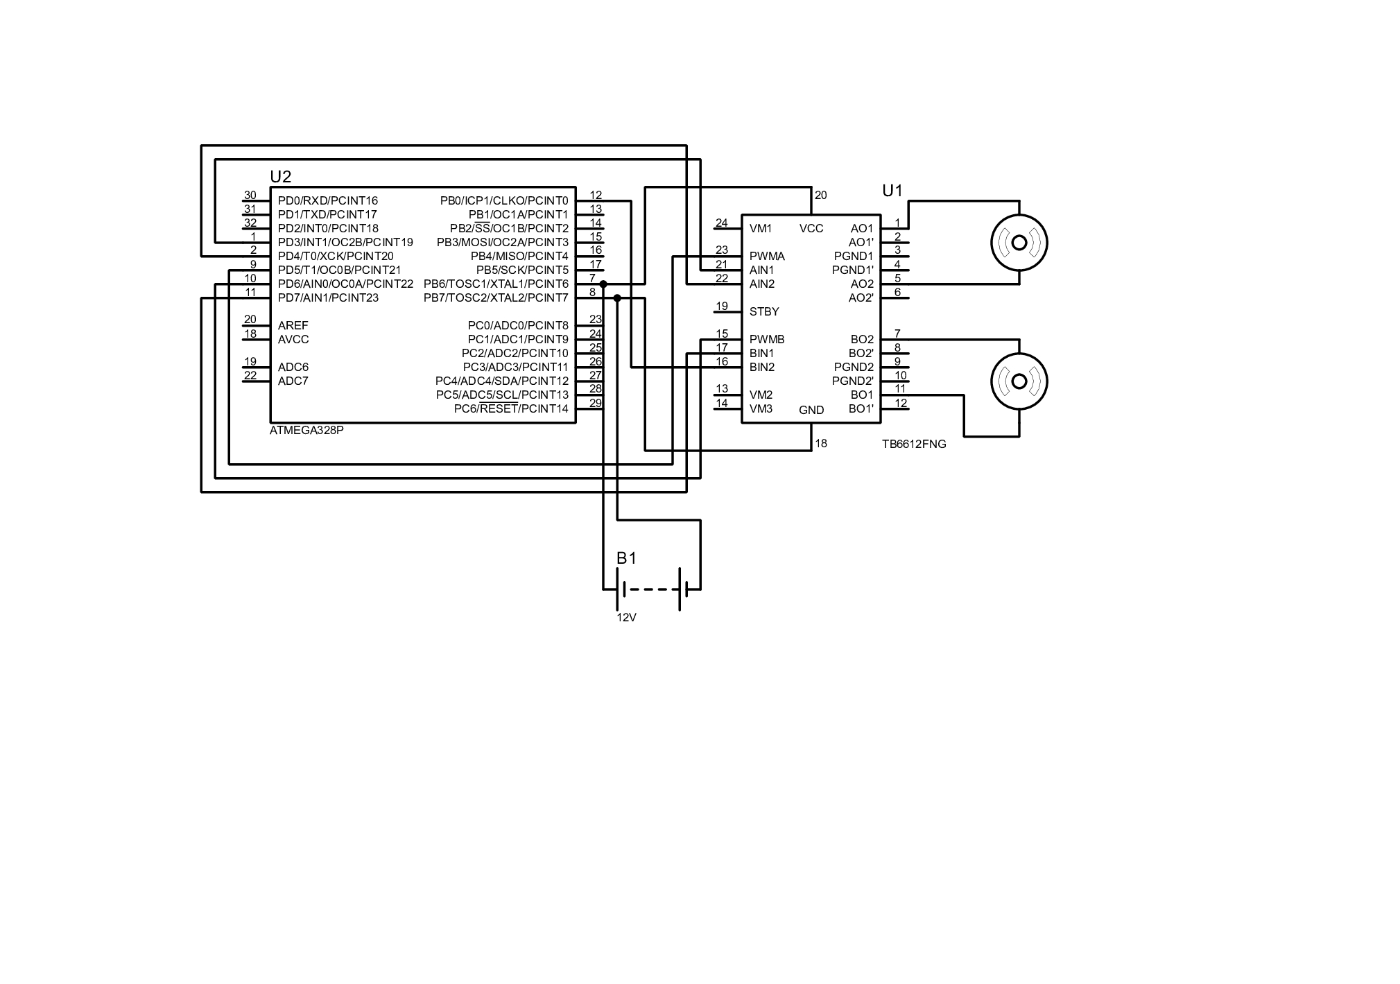
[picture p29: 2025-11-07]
electronics/img/Semana 1/circuito prototipo no proteus.jpg

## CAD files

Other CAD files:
mechanics/Sr. Batata.ipt
mechanics/aramdura_sr_batata.ipt
mechanics/img/Semana 2/MiniSumo 10x10.ipt
mechanics/img/Semana 2/Rampa 1.ipt
mechanics/img/Semana 2/Sr. Batata.ipt

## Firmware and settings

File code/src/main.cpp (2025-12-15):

//Bibliotecas//


#include <Bluepad32.h>


ControllerPtr meusControles[BP32_MAX_GAMEPADS];


//Entradas na ESP32 e Variáveis//


#define A11 25   //Esquerda Frente
#define A12 33   //Esquerda Trás
#define PWNA 13  //Esquerda Potência


#define B11 26   //Direita Frente
#define B12 27   //Direita Trás
#define PWNB 14  //Direita Potência


#define BUZZER 19


int VELOCIDADE =255;
int i;


//Setup//




void setup() {
  Serial.begin(115200);


  pinMode(PWNA, OUTPUT);
  pinMode(A11, OUTPUT);
  pinMode(A12, OUTPUT);


  pinMode(PWNB, OUTPUT);
  pinMode(B11, OUTPUT);
  pinMode(B12, OUTPUT);


  pinMode(BUZZER, OUTPUT);


  BP32.setup(&onConnectedController, &onDisconnectedController);


}


//Estabelece a conexão segura com os controles e os salva na matriz//




void onConnectedController(ControllerPtr ctl) {
  for (int i = 0; i < BP32_MAX_GAMEPADS; i++) {
    if (meusControles[i] == nullptr) {
      tone(BUZZER,2500);
      delay(1000);
      noTone(BUZZER);
      delay(200);
      meusControles[i] = ctl;
      break;
    }
  }
}


//Desconenecta os controles e os retira da matriz//




void onDisconnectedController(ControllerPtr ctl) {
  for (int i = 0; i < BP32_MAX_GAMEPADS; i++) {
    if (meusControles[i] == ctl) {
      meusControles[i] = nullptr;
      break;
    }
  }
}


//Confirma a conexão do dispositivo, seu tipo e os dados nele, o transmitindo os comandos do controle vindos do código//


void processaTodosControles() {
  for (auto ctl : meusControles) {
    if (ctl && ctl->isConnected() && ctl->hasData()) {
      if (ctl->isGamepad()) {
         processaControle(ctl);
      }
    }
  }
}


//Comandos do controle//


void processaControle(ControllerPtr ctl) {


  if(ctl->axisY() >= 30) {
    digitalWrite(A11, HIGH);                //Roda esquerda frente
    digitalWrite(A12, LOW);
    analogWrite(PWNA, VELOCIDADE);


  }


  else if(ctl->axisY() <= -30) {
    digitalWrite(A11, LOW);                 //Roda esquerda trás
    digitalWrite(A12, HIGH);
    analogWrite(PWNA, VELOCIDADE);
  }


  else {
    digitalWrite(A11, LOW);                 //Deadzone esquerda
    digitalWrite(A12, LOW);
    analogWrite(PWNA, 0);
  }




  if(ctl->axisRX() >= 30) {
    digitalWrite(B11, HIGH);                //Roda direita frente
    digitalWrite(B12, LOW);
    analogWrite(PWNB, VELOCIDADE);


  }


  else if(ctl->axisRY() <= -30) {
    digitalWrite(B11, LOW);                 //Roda direita trás
    digitalWrite(B12, HIGH);
    analogWrite(PWNB, VELOCIDADE);


  }


  else {
    digitalWrite(B11, LOW);                 //Deadzone direita
    digitalWrite(B12, LOW);
    analogWrite(PWNB, 0);


  }

  if (ctl->b()){
    for(i=0; i<3; i++){
      tone(BUZZER,2000);                    //Apito
      delay(150);
      noTone(BUZZER);
      delay(200);
    }
  }
}


//Função Principal//




void loop() {
  bool dataUpdated = BP32.update();
  if (dataUpdated){
    processaTodosControles();
    delay(150);
  }


}

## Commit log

2025-11-07 Adição do primeiro esquema eletrônico
    Utilizamos o chip do arduino nano somente para ter uma ideia
2025-11-07 Adição de alguns modelos 3D do nosso Robô
    Adicionando o modelo Sr Batata, que é a base principal do robô, e uma das rampas
    [Rampa 1.ipt, Sr. Batata.ipt]
2025-11-07 Modificando o modelo da primeira rampa
    [Rampa 1.ipt]
2025-11-14 Teste de commit
2025-11-14 Teste de commit 2
2025-11-14 Modificação do README de Eletrônica
2025-11-18 Adição de imagens de eletrônica
2025-11-18 Adicionando documentação criada por Vitória
    [encontros semanais.xlsx]
2025-11-24 Adicionando arquivo mini_sumô 10x10
    [MiniSumo 10x10.ipt]
2025-12-02 Add files via upload
    ata de reuniao
2025-12-12 Atualizando com imagens e descrições
    [encontros semanais.xlsx]
2025-12-12 Atualizando documentação
    [MiniSumo 10x10.ipt, Rampa 1.ipt, Sr. Batata.ipt]
2025-12-15 Mudando coisas de mecanica
    [MiniSumo 10x10.ipt, Rampa 1.ipt, Sr. Batata.ipt]
2025-12-15 Mudando o readme do codigo
    [encontros semanais.xlsx]
2025-12-15 Mudando o readme de programação
2025-12-15 Mudando o readme de programacao dnv
2025-12-15 Colocando os arquivos do srBatata utilizado no dia da batalha
    [Sr. Batata.ipt, aramdura_sr_batata.ipt]
2025-12-15 Mudando o readme de docs
